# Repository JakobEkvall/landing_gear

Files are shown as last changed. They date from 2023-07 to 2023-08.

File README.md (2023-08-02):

# landing_gear
PCB for the Shafter quadrotor landing platforms stepper motor and limit switches. 

Schematics and PCB designed with KiCad. 

Mouser cart for the needed components: https://www.mouser.se/ProjectManager/ProjectDetail.aspx?AccessID=22832bf478

The core of the circuit is an Atmega328P, set up in the same way as the Arduino Nano MCU with a USB connection. 

Stepper motor is driven with a DRV8825 IC.

Limit switches are active LOW.

The whole circuit is powered with a battery, minimum input voltage should be around 8V (otherwise the stepper motor driver will not work) and the maximum battery voltage should not exceed 15V, otherwise the 5V regulator could be damaged. Heatsinks might be needed for the stepper driver IC and the 5V regulator, depending on the input battery voltage and the power consumption of the stepper motor. 

Two resistors on the PCB, R3 and R4, do not have values as that depends on the specific model of  stepper motor used and other factors, see section 8.3.2 in the datasheet for further information on resistor value selection https://www.ti.com/lit/ds/symlink/drv8825.pdf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. 

 All of the digital pins on the stepper motor IC are routed to pins on the microcontroller, so MODE and DECAY etc will have to be defined in code and is not preset.

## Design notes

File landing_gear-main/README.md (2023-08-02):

# landing_gear
PCB for the Shafter landing platforms stepper motor and limit switches. 

Schematics and PCB designed with KiCad. 

Mouser cart for the needed components: https://www.mouser.se/ProjectManager/ProjectDetail.aspx?AccessID=22832bf478

A1, A2, B1, B2 correspond to the A1, A2 etc pins on the DRV8825 stepper motor driver, and are the connection points for a four wire stepper motor. 

HIGH and LOW are the two limit switches inputs, with corresponding GND pads for each.

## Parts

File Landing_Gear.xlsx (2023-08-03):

Id | Designator | Footprint | Quantity | Designation | Supplier and ref
1 | R3,R4 | R_0603_1608Metric | 2 | R | Value depends on stepper motor used, which is unknown to me at the moment. Footprint is 0603 surface mount capacitor.
2 | U3 | SSOP-28_5.3x10.2mm_P0.65mm | 1 | FT232RL | https://www.mouser.se/ProductDetail/FTDI/FT232RNL-REEL?qs=By6Nw2ByBD3LSfXryh9qRQ%3D%3D
3 | R9,R5,R6 | R_0603_1608Metric | 3 | 10k | https://www.mouser.se/ProductDetail/ROHM-Semiconductor/KTR03EZPF1002
4 | C18,C17 | C_0603_1608Metric | 2 | 22pF | https://www.mouser.se/ProductDetail/KEMET/C0603C220K3RACAUTO?qs=sGAEpiMZZMuMW9TJLBQkXhFFl7Eqwd3UDl1LMiUfdmA%3D
5 | C12 | C_0603_1608Metric | 1 | 470nF | https://www.mouser.se/ProductDetail/TAIYO-YUDEN/UMK107B7474KA-TR
6 | J3,J4 | PinHeader_1x04_P2.54mm_Vertical | 2 | Conn_01x04 | none
7 | R1,R8,R7 | R_0603_1608Metric | 3 | 1k | https://www.mouser.se/ProductDetail/Bourns/CHP0603QFX-1001ELF
8 | C16,C14 | C_0603_1608Metric | 2 | 1uF | https://www.mouser.se/ProductDetail/KYOCERA-AVX/06035C105KAT2A
9 | C13,C11,C10,C5,C7,C3,C8 | C_0603_1608Metric | 7 | 100nF | https://www.mouser.se/ProductDetail/KEMET/C0603C104K1RACAUTO?qs=sGAEpiMZZMuMW9TJLBQkXrHql0md5dKl6w87yrT8Awo%3D
10 | U1 | TO-252-3_TabPin2 | 1 | LM1117DT-5.0 | https://www.mouser.se/ProductDetail/Texas-Instruments/LM1117DT-5.0-NOPB?qs=X1J7HmVL2ZGITaQRKQ6NVA%3D%3D
11 | C2,C6 | CP_Elec_4x4.5 | 2 | 10uF | https://www.mouser.se/ProductDetail/Nichicon/UCQ1C100MCL1GB?qs=55YtniHzbhAF7rDcdgu07w%3D%3D
12 | D1 | LED_0805_2012Metric | 1 | LED | https://www.mouser.se/ProductDetail/Wurth-Elektronik/150080BS75000?qs=2kOmHSv6VfT2tBo3UPVqAQ%3D%3D
13 | C9 | C_0603_1608Metric | 1 | 10nF | https://www.mouser.se/ProductDetail/KYOCERA-AVX/06036C103KAT4A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
14 | C4,C15 | CP_Elec_4x4.5 | 2 | 4.7uF | https://www.mouser.se/ProductDetail/Nichicon/UCQ1E4R7MCL1GB?qs=55YtniHzbhCY6EpSWZ22lg%3D%3D
15 | F1 | Fuse_1812_4532Metric | 1 | MF-MSMF050-2 | https://www.mouser.se/ProductDetail/Bourns/MF-MSMF050-2?qs=t3shhpq1i1DZ7OBD5kLNoA%3D%3D
16 | Y1 | Crystal_SMD_3225-4Pin_3.2x2.5mm | 1 | 16MHz | https://www.mouser.se/ProductDetail/ABRACON/ABM8-16.000MHZ-9-D1G-T?qs=vLWxofP3U2zvRnDcNI29iQ%3D%3D
17 | SW1 | SW_SPST_Omron_B3FS-100xP | 1 | SW_Push | https://www.mouser.se/ProductDetail/Omron-Electronics/B3FS-1000P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
18 | H1,H2 | MountingHole_3.2mm_M3 | 2 | MountingHole | none
19 | J1 | USB_Micro-B_GCT_USB3076-30-A | 1 | USB_B_Micro | https://www.mouser.se/ProductDetail/GCT/USB3076-30-A?qs=KUoIvG%2F9IlZs3NcnVJVajg%3D%3D
20 | C1 | CP_Elec_4x4.5 | 1 | 100uF | https://www.mouser.se/ProductDetail/Nichicon/UZS0G101MCL1GB?qs=huzeVNXgovWXqYnJaB9VQQ%3D%3D
21 | U4 | TQFP-32_7x7mm_P0.8mm | 1 | ATmega328P-A | https://www.mouser.se/ProductDetail/Microchip-Technology/ATMEGA328P-AU?qs=K8BHR703ZXiCmmgp6%2FGNmQ%3D%3D
22 | D2 | D_SOD-523 | 1 | RB520SM | https://www.mouser.se/ProductDetail/ROHM-Semiconductor/RB520SM-40T2R?qs=IsRgwgmxh6%252BY8Wb1Xyc5mw%3D%3D
23 | U2 | DRV8825 | 1 | DRV8825 | https://www.mouser.se/ProductDetail/Texas-Instruments/DRV8825PWP?qs=L4ss%2FyqpMWT%252BKNufX9tf3Q%3D%3D
24 | RV1 | Potentiometer_Bourns_3314J_Vertical | 1 | 10k | https://www.mouser.se/ProductDetail/Bourns/3314Z-1-103E
25 | R2 | R_0603_1608Metric | 1 | 1M | https://www.mouser.se/ProductDetail/KOA-Speer/HV731JRTTD1004F
26 | J2 | Battery holes | 1 | Conn_01x02 | none

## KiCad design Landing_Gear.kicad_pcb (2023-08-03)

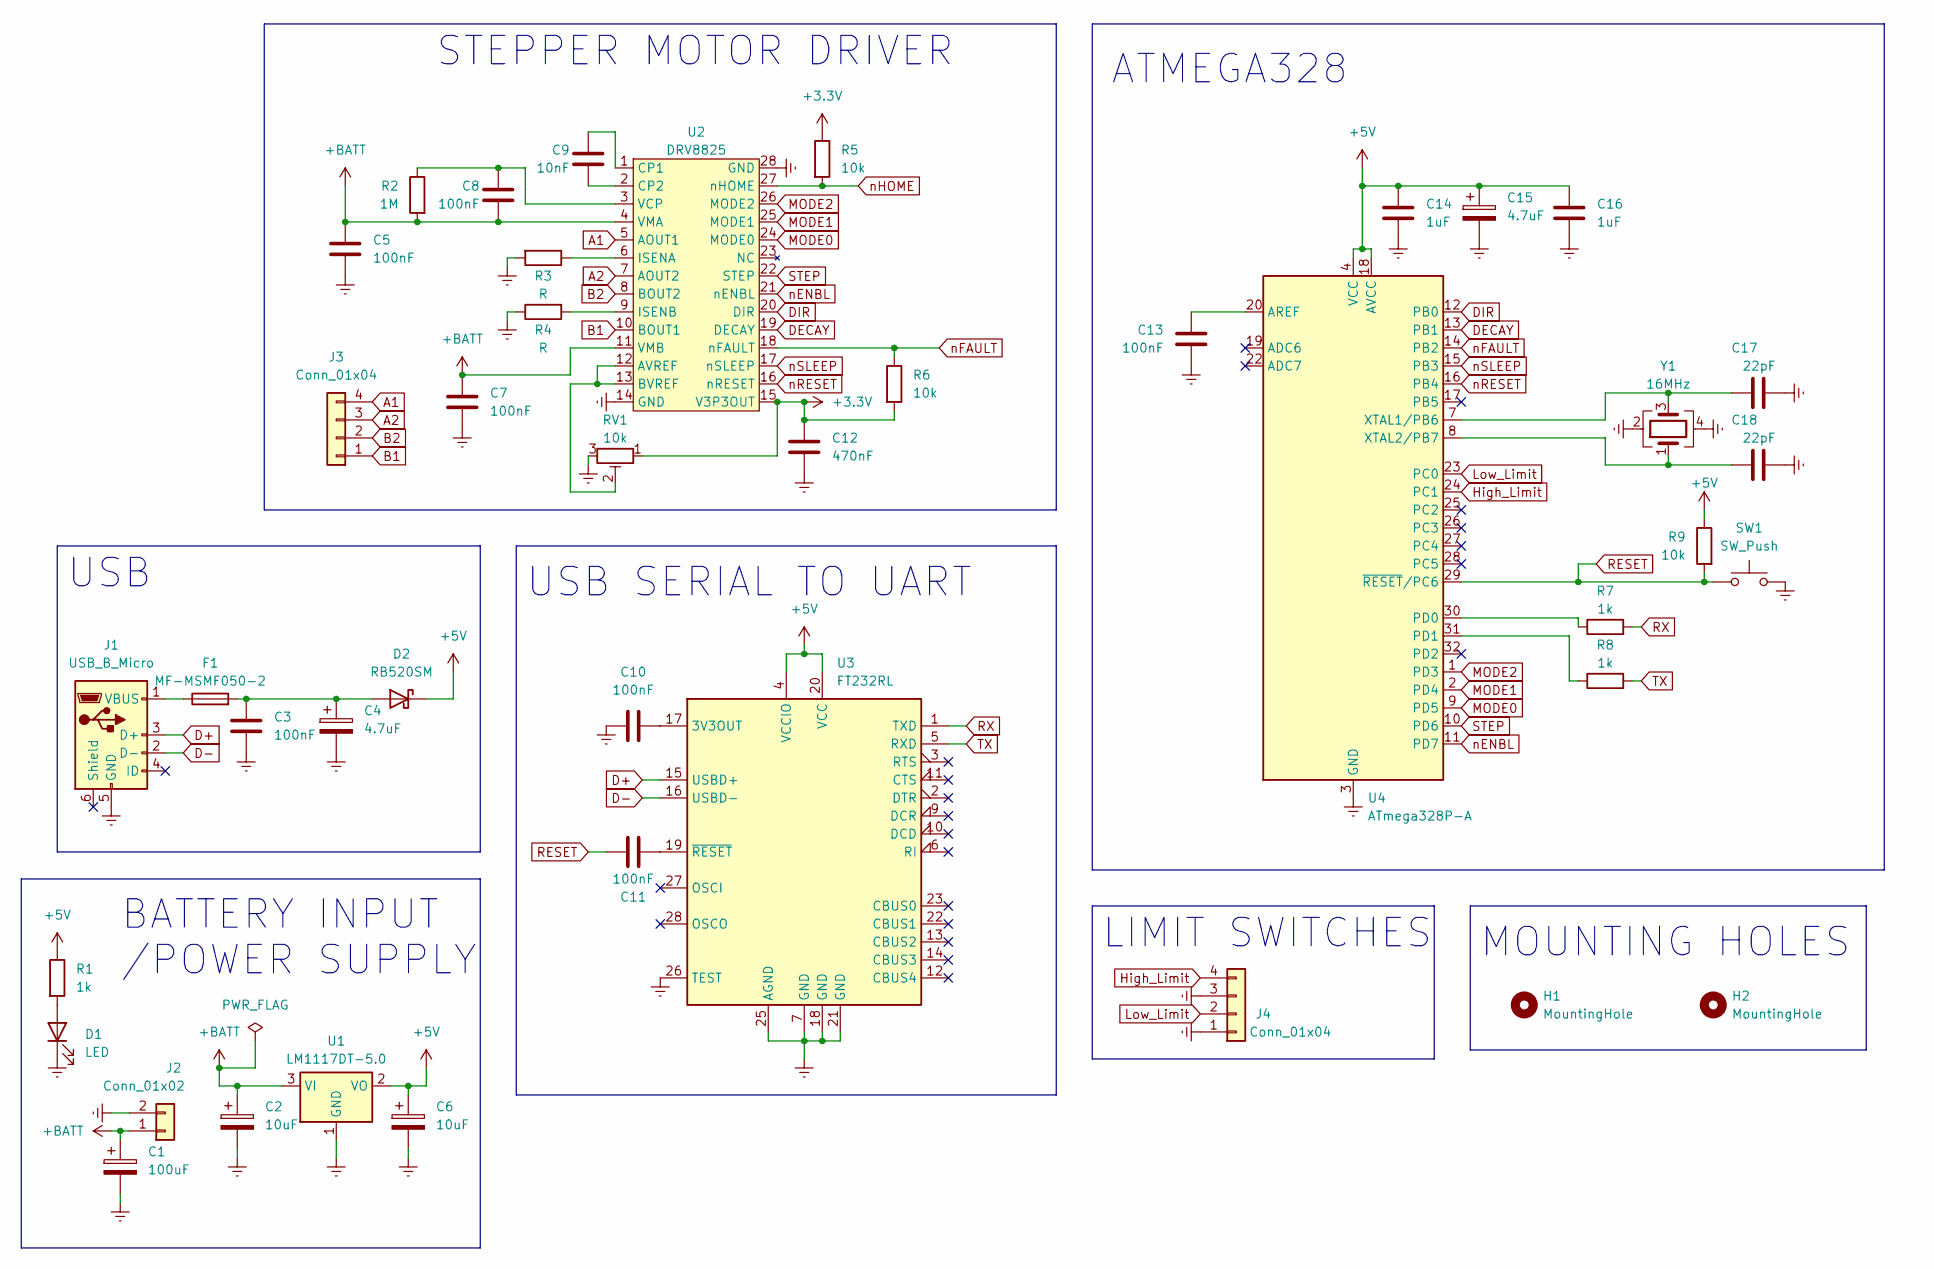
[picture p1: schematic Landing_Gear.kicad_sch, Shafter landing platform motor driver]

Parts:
C1: 100uF; CP_Elec_4x4.5
C2, C6: 10uF; CP_Elec_4x4.5
C3, C5, C7, C8, C10, C11, C13: 100nF; C_0603_1608Metric
C4, C15: 4.7uF; CP_Elec_4x4.5
C9: 10nF; C_0603_1608Metric
C12: 470nF; C_0603_1608Metric
C14, C16: 1uF; C_0603_1608Metric
C17, C18: 22pF; C_0603_1608Metric
D1: LED; LED_0805_2012Metric
D2: RB520SM; D_SOD-523
F1: MF-MSMF050-2; Fuse_1812_4532Metric
H1, H2: MountingHole; MountingHole_3.2mm_M3
J1: USB_B_Micro; USB_Micro-B_GCT_USB3076-30-A
J2: Conn_01x02; Battery holes
J3, J4: Conn_01x04; PinHeader_1x04_P2.54mm_Vertical
R1, R7, R8: 1k; R_0603_1608Metric
R2: 1M; R_0603_1608Metric
R3, R4: R; R_0603_1608Metric
R5, R6, R9: 10k; R_0603_1608Metric
RV1: 10k; Potentiometer_Bourns_3314J_Vertical
SW1: SW_Push; SW_SPST_Omron_B3FS-100xP
U1: LM1117DT-5.0; TO-252-3_TabPin2
U2: DRV8825
U3: FT232RL; SSOP-28_5.3x10.2mm_P0.65mm
U4: ATmega328P-A; TQFP-32_7x7mm_P0.8mm
Y1: 16MHz; Crystal_SMD_3225-4Pin_3.2x2.5mm

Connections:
+3.3V: C12.1, R5.1, R6.2, RV1.1, U2.15 (V3P3OUT)
+5V: C6.1, C14.1, C15.1, C16.1, D2.1 (K), R1.1, R9.1, U1.2 (VO), U3.4 (VCCIO), U3.20 (VCC), U4.4 (VCC), U4.6 (VCC), U4.18 (AVCC)
+BATT: C1.1, C2.1, C5.1, C7.1, C8.2, J2.1, R2.2, U1.3 (VI), U2.4 (VMA), U2.11 (VMB)
A1: J3.4, U2.5 (AOUT1)
A2: J3.3, U2.7 (AOUT2)
B1: J3.1, U2.10 (BOUT1)
B2: J3.2, U2.8 (BOUT2)
D+: J1.3 (D+), U3.15 (USBD+)
D-: J1.2 (D-), U3.16 (USBD-)
DECAY: U2.19 (DECAY), U4.13 (PB1)
DIR: U2.20 (DIR), U4.12 (PB0)
Earth: C1.2, C2.2, C3.2, C4.2, C5.2, C6.2, C7.2, C10.1, C12.2, C13.2, C14.2, C15.2, C16.2, C17.2, C18.2, D1.1 (K), J1.5 (GND), J2.2, J4.1, J4.3, R3.2, R4.1, RV1.3, SW1.2, U1.1 (GND), U2.14 (GND), U2.28 (GND), U3.7 (GND), U3.18 (GND), U3.21 (GND), U3.25 (AGND), U3.26 (TEST), U4.3 (GND), U4.5 (GND), U4.21 (GND), Y1.2, Y1.4
High_Limit: J4.4, U4.24 (PC1)
Low_Limit: J4.2, U4.23 (PC0)
MODE0: U2.24 (MODE0), U4.9 (PD5)
MODE1: U2.25 (MODE1), U4.2 (PD4)
MODE2: U2.26 (MODE2), U4.1 (PD3)
unnamed: D1.2 (A), R1.2
unnamed: C3.1, C4.1, D2.2 (A), F1.2
unnamed: F1.1, J1.1 (VBUS)
unnamed: RV1.2, U2.12 (AVREF), U2.13 (BVREF)
unnamed: C9.1, U2.1 (CP1)
unnamed: C9.2, U2.2 (CP2)
unnamed: R3.1, U2.6 (ISENA)
unnamed: R4.2, U2.9 (ISENB)
unnamed: C8.1, R2.1, U2.3 (VCP)
unnamed: C10.2, U3.17 (3V3OUT)
unnamed: C11.2, U3.19 (~RESET)
unnamed: C13.1, U4.20 (AREF)
unnamed: R7.1, U4.30 (PD0)
unnamed: R8.1, U4.31 (PD1)
unnamed: C17.1, U4.7 (XTAL1/PB6), Y1.3
unnamed: C18.1, U4.8 (XTAL2/PB7), Y1.1
RESET: C11.1, R9.2, SW1.1, U4.29 (~RESET/PC6)
RX: R7.2, U3.1 (TXD)
STEP: U2.22 (STEP), U4.10 (PD6)
TX: R8.2, U3.5 (RXD)
nENBL: U2.21 (nENBL), U4.11 (PD7)
nFAULT: R6.1, U2.18 (nFAULT), U4.14 (PB2)
nHOME: R5.2, U2.27 (nHOME)
nRESET: U2.16 (nRESET), U4.16 (PB4)
nSLEEP: U2.17 (nSLEEP), U4.15 (PB3)

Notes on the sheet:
LIMIT SWITCHES
USB
USB SERIAL TO UART
ATMEGA328
MOUNTING HOLES
STEPPER MOTOR DRIVER
BATTERY INPUT /POWER SUPPLY

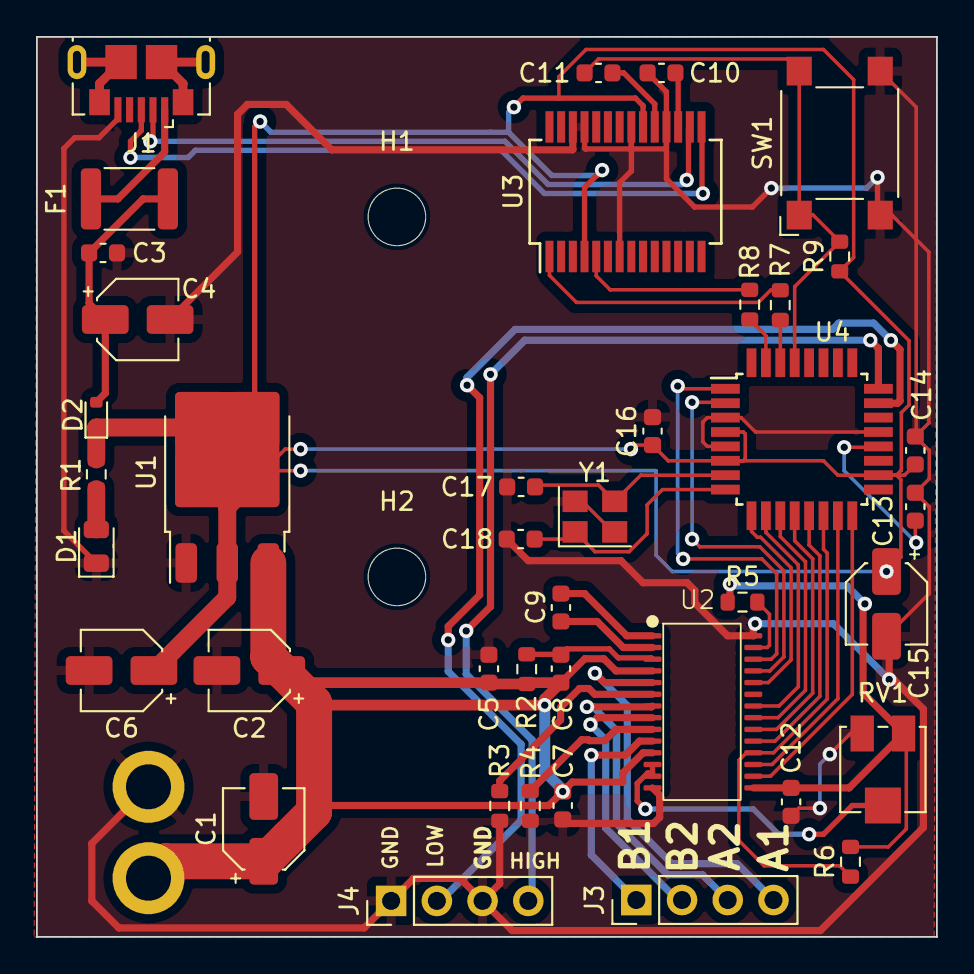
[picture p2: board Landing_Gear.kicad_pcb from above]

Board: 2 copper layers, 50.0 x 50.0 mm, 43 parts (1 on the bottom side), 42 nets.
